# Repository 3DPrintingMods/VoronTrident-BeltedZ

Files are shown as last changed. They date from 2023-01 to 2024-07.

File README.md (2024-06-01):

<br/>
<p align="center">
  <h3 align="center">Voron Trident Belted Z</h3>

  <p align="center">
    Belt all the things.
    <br/>
    <br/>
  </p>
</p>

## About The Project

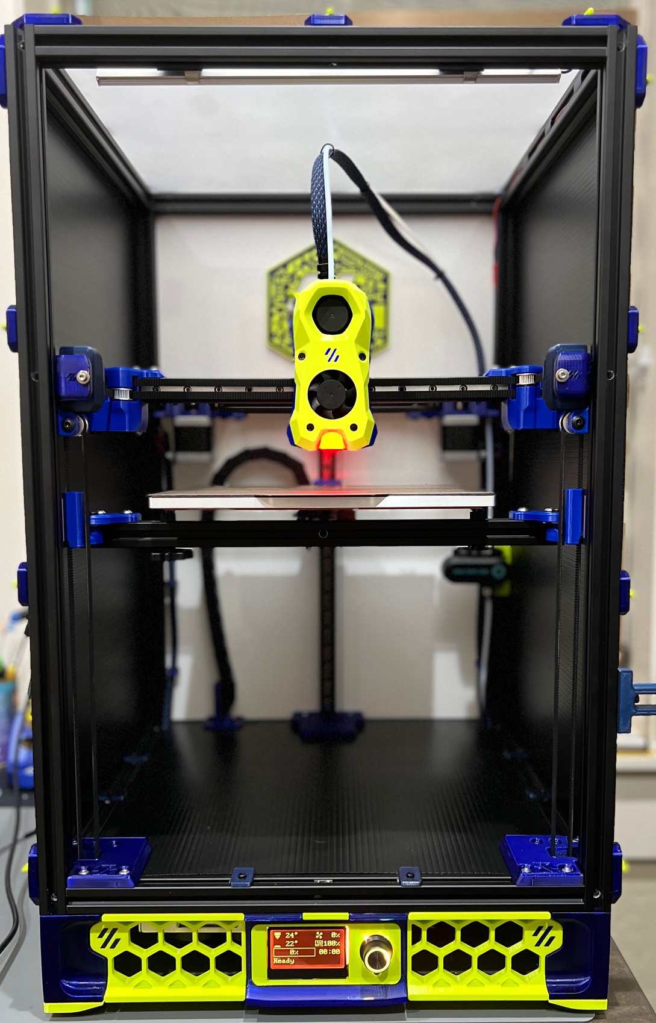
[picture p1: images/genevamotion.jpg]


This `mod` is the combination of multiple ideas for belted system for the Trident Z motion. Most of the inspiration came from X0, which uses NEMA 17 gearboxes. The main goal was to use 9mm belts for Z motion while keeping most of the original Trident skirts and not relocating Z steppers to the top of the printer. We give credit to `bythorsthunder` for his [Orion belted mod](https://github.com/bythorsthunder/Orion-Tri-Belt), which has also been proven efficient and easy to assemble (the same applies to the [belted z motion](https://github.com/MathematicalPotato/Voron_Mods/tree/main/VT_Belted_Z) mod introduced by `MathematicalPotato`).

## General Info

The design offers two different options for the Z idlers:

MathmaticalPotato Idlers: 
 - Uses existing XY front idlers
 - Limited to ONLY 9mm wide pulleys (12mm overall width)
<p align="left">
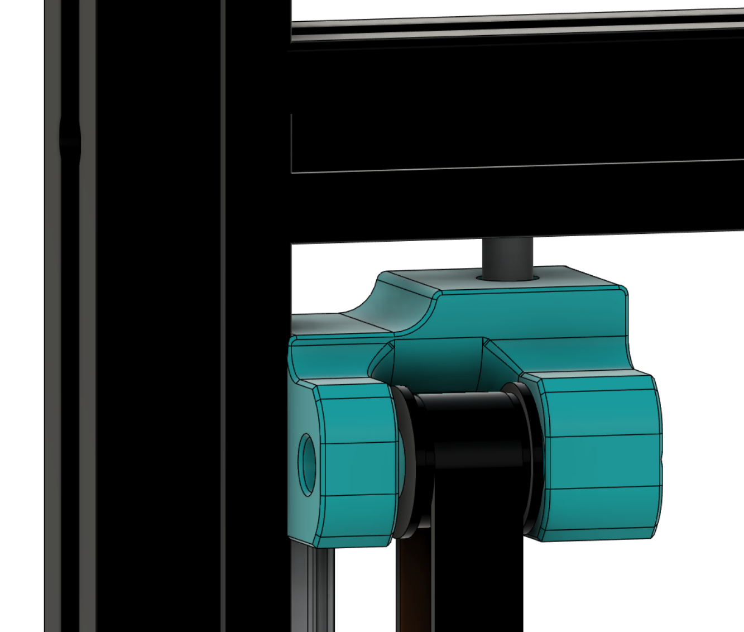
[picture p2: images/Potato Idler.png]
  
</p>

DoubleT XYZ Idlers:
 - Modified version of the Ramalama2 idler design
 - Z idler pulley integrated into XY idler
 - More flexibility in Z pulley width
<p align="left">
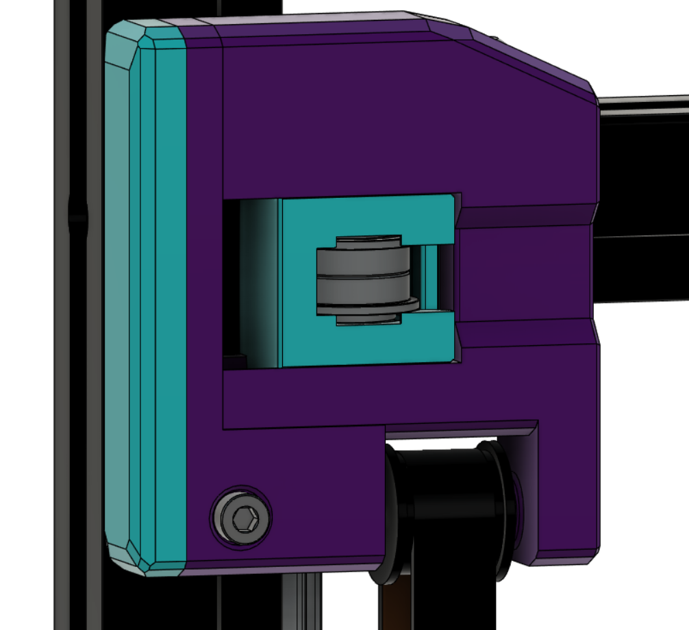
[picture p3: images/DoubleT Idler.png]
  
</p>

Refer to the CAD drawing for detail on both Idlers.
BOM contains sections for both.

## Update History:

#May 31st 2024
 - Added motor mounts and skirts for larger gearbox 'precision' motors
 - NOTE:  These motors are recommended for larger bed sizes 300+
 - Added Z idlers for DoubleT / Fabreeko 9MM metal gantry

#April 2024
 - Monolith Gantry Support added

#November 30th 2023
 - V2 Beta idlers added

#October 12th 2023
 - Raised the bed standoffs on the carriages by 6mm.
 - This should improve compatibility with slimmer beds and most iterations of Tiny-T.
 - NOTE: Requires a change from M5x16 to M5x25 fasteners for the carriage to the bed frame.

#July 23rd 2023 
 - Added belt/stepper covers for inverted electronics by `Panzarkatten`

#July 3rd 2023:
 - Revised rear motor mount and idler.  Orientation of the motor turned 90 degrees. New idler replaces the rear bracing from Z extrusion to A/B drive extrusion
 - New front idler option added. Integrated the Z idler pulley into DoubleT's modified Rama idlers.
 - Cleaned up the CAD
 - Added motor skirts for 350mm build size

## Tiny-T considerations:
The Tiny-T supports the use of either MGN9 or MGN12 linear guides on the X axis.  This mod is compatible with MGN12 / Afterburner/Stealthburner style toolheads without modificaiton.
MGN9 based systems using V0.2 style toolheads will position the nozzle 5-6mm higher than AB/SB configurations.  This results in the bed being unable to reach the nozzle before colliding with the Z idlers. V3 Z carriages should resolve this travel limitation, but this assumes the use of a 6mm build plate with a 1mm magnet.  Magbeds may need additional spacing.

## Bill Of Materials

#Required parts:

- 3 NEMA 17 Precision planetary steppers
	 - Recommended for larger bed sizes.
	 - Higher Gear Ratio, lower backlash
	 - [OMC Stepperonline](https://www.omc-stepperonline.com/nema-17-stepper-motor-l-40mm-gear-ratio-10-1-mg-series-planetary-gearbox-17hs15-1584s-mg10)
*or*
- 3 NEMA 17 Economy planetary steppers
	- [Ali Express](https://www.aliexpress.us/item/3256804434852612.html)
	- [Amazon](https://www.amazon.com/STEPPERONLINE-Planetary-Gearbox-Stepper-Printer/dp/B00WATUFIG)

- 9mm GT2 belts
- 3 9mm 20T GT2 drive pulleys, 8mm ID
- 3 9mm 20T toothed idlers, 5mm ID - Gates/Runice recommended. (Overall width of less than 14mm, Flange diameter less than 16mm)
- 9 M3x12 Button head screws (mounting gearmotors)
- 8 M3x30 Socket head screws (Front Motor Bracing, Rear Z carriage mounting)
- 2 M3x35 screws (Front Z belt tensioners)
- 1 M3x40 screw (Rear Z belt tensioner)
- 7 M3 heatset inserts (Front motor bracing, Z belt tensioners)
- 2 M5x35 screws and nuts (front idlers)
- 1 M5x25 screw and nut (rear idler)
- 1 5mmx30mm dowel (Rear Z Idler Shaft)
- 20 M5x10 screws and hammerhead nuts for mounting motor mounts and idlers
- 1 M3 x ? length screw - Length determined by motor chosen. Remove one screw from the nema17 motor housing and replace with longer screw for the rear motor stabilizer.
- 3 M5x25 BHCS - Z carriage to bed frame

<p align="left">
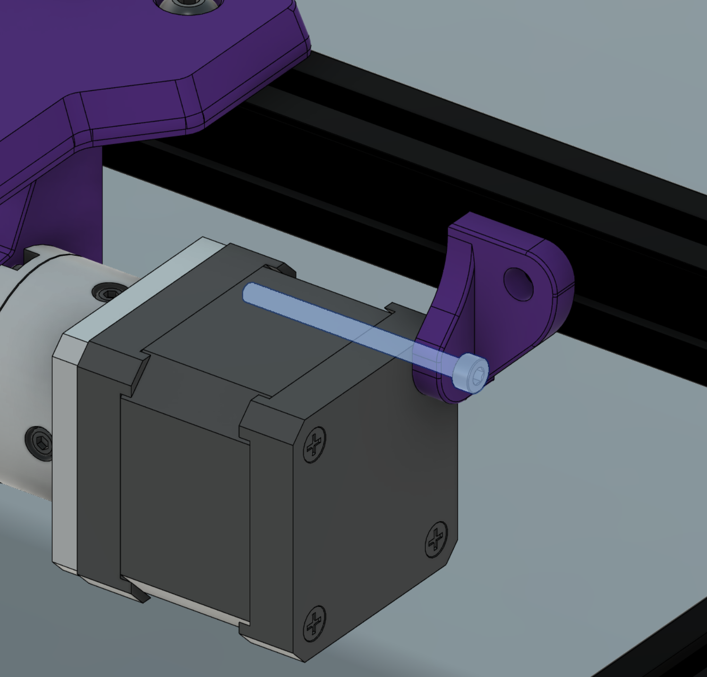
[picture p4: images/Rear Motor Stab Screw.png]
  
</p>

Mathematical Potato Idlers:
- 2 M4x20 Socket head screws and hammerhead nuts
- 2 M5x40 Button head screws
- 2 M5 nuts
- 2 M5x15 Button Head Screws

DoubleT XYZ Idlers
 - Reuses existing fasteners for securing idler to Y extrusion
- 4 M3 heatset inserts
- 4 M3x30 Button head screws
- 2 M3x12 Socket head screws
- 2 M3x20 Socket head screws and hammerhead nuts
- 2 5mm x 25mm dowel
- 2 5mm x 20mm dowel
- 4 6mm x 3mm magnets

## Authors

* **genevamotion** - ** - [genevamotion](https://github.com/tdlane1) - *CAD design/ Modeling / Testing*
* **thiagolocatelli** - ** - [thiagolocatelli](https://github.com/thiagolocatelli) - *CAD design / Modeling / Project Management*

## Acknowledgements

* [MathematicalPotato](https://github.com/MathematicalPotato)
* [bythorsthunder](https://github.com/bythorsthunder)
* [Annex Engineering](https://github.com/Annex-Engineering)
* [Voron Design](https://github.com/VoronDesign)
* [Ramalama](https://github.com/Ramalama2)
* [clee](https://github.com/clee/VoronBFI)

## Images

<p align="center">
  
</p>

<p align="center">
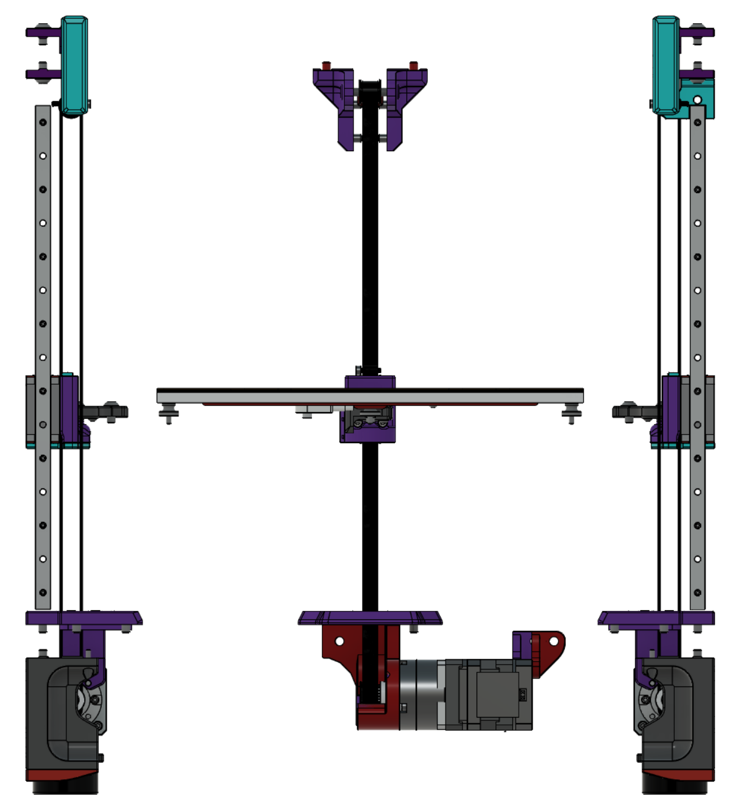
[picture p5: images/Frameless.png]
  
</p>

<p align="center">
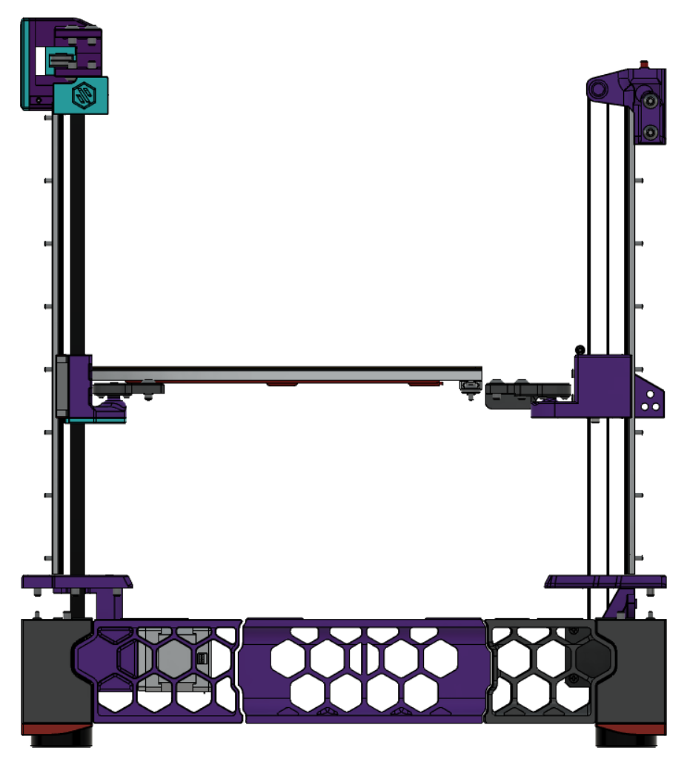
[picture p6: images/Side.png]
  
</p>

<p align="center">
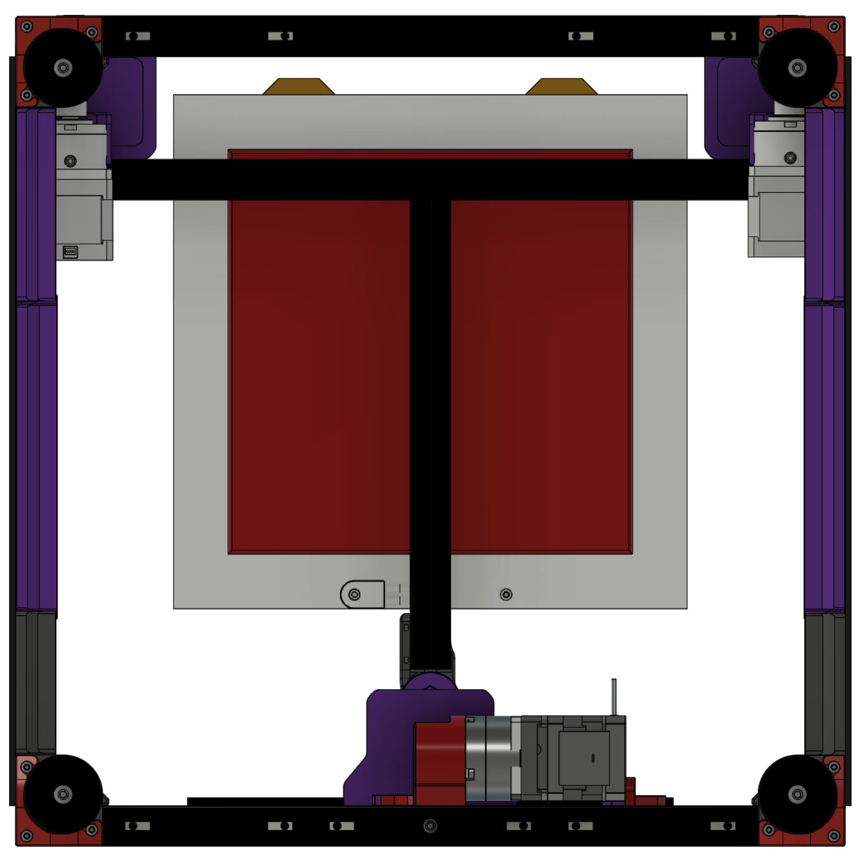
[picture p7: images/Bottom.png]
  
</p>

<p align="center">
  
</p>

## Sample config (Manta M8P) - Economy Gearbox 

```
[stepper_z]
step_pin: ###
dir_pin: ###
enable_pin: ###
rotation_distance: 40
gear_ratio: 57:11   
microsteps: 32
endstop_pin: ###

##  Make sure to update below for your relevant driver (2208 or 2209)
[tmc2209 stepper_z]
uart_pin: ###
interpolate: False
run_current: 1.0
sense_resistor: 0.110
stealthchop_threshold: 0

```

# Builds

## Panzarkatten

<p align="center">
  
</p>

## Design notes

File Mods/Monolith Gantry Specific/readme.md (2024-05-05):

## BeltedZ components for Monolith Gantry

These parts were created for compatibility with [Monolith Gantry](https://github.com/CloakedWayne/Monolith_Gantry_V2-VT).  No changes are needed to the monolith gantry components. The mod includes modified Z idlers and *optional* Z carriages that relocate the bed 10mm in the +Y direction.  

The Notes and BOM differences may leave out critical information. These BOM differences are in relation to the BeltedZ mod, and not stock Voron components.  Apologies in advance if items were left out.

I'm lazy - Printing orientation has not been preset on many parts, but it's fairly obvious in most cases which side is down.

## Idler Notes

 - The front Z idlers currently use M5x45 screws as shafts for the idler pulleys to ride on.  This isn't a perfect solution, and a dowel-pin version is on the horizon.
 - The front Z linear guides will obstruct insertion and removal of the front-most fasteners that secure the idlers to the Y extrusions.  It is recommended that you install the front XY and Z idler assemblies **before** the Y linear guides.  This will allow the idler assembly to be slid along the Y extrusion for access to insert the fastener, and slid back into place for before final tightening of the fasteners.  Alternatively, you can remove the Z linear guide for access, but in most cases you will already have the Y linear guides removed during conversion to Monolith Gantry.
 - The rear Z idler has notches for the Monolith AB tensioners to clear, as well as provide access to the tensioning screws. These notches aren't needed in 250+ builds, but with Tiny-T they are necessary.
 - AWD idler spacers are provided.  These are needed to space the Z idler lower so that it can clear the shear support plates of the front motor mounts. Longer fasteners are needed to secure the idlers to the Y extrusions.
 - You may notice the front Z idlers have a circular relief in the top side that goes nowhere. This is to provide clearance for a fastener that may be present on the monolith front motorless mounts. BHCS is assumed in this case, and the fastener may need to be changed to fit the relief.

**Idler BOM Differences**

 - Idlers (2WD):
	 - 4x M5x16 
	 - 2X M5x20
	 - 2X M5x45

- Idlers (AWD):
	- 6x M5x20
	- 2X M5x45

## Bed +10 Notes
*Why relocate the bed?* - This isn't necessary, but some toolhead designs will place the hotend nozzle as close to the X axis linear rail carriage as possible to improve balance and center of mass. The front edge of the bed may be out of reach with stock carriages in this scenario.

 - A modified Z_Bed_Rear model is provided.  This part needs to be printed, as the stock Voron rear bed extrusion attachement interferes with the belt.  It has clearance for the belt as well as relocated fasteners that secure the spherical bearing to the part.
 - Z carriages elevate the bed 5mm over stock to reach PFA style toolheads on Tiny-T.  Verify total Z travel distance after completion as the new carriages have probably affected it.

**Z Carriage BOM Differences**

 - 4x M3x20
- 8x M3x25
- 3x M5x25

## Acknowledgements:

 - The BeltedZ mod was heavily inspired by MathematicalPotato's [VT_Belted_Z](https://github.com/MathematicalPotato/Voron_Mods/tree/main/VT_Belted_Z) mod
 - [CloakedWayne](https://github.com/CloakedWayne) - Monolith Gantry

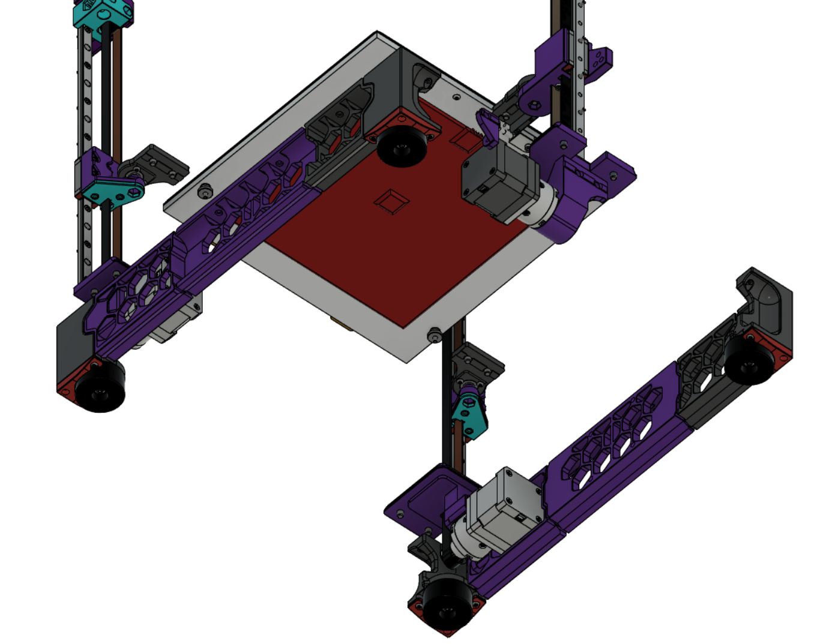
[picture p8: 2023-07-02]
images/Bottom Iso.png

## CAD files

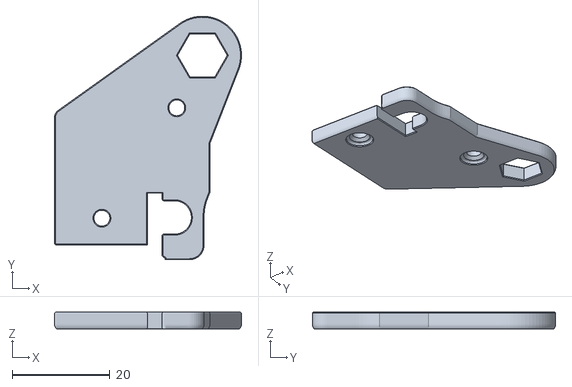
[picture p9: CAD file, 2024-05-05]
Mods/Monolith Gantry Specific/STL/Bed_Plus_10MM/Z_Carriage_Accent_L.stl
38.2 x 49.8 x 3.45

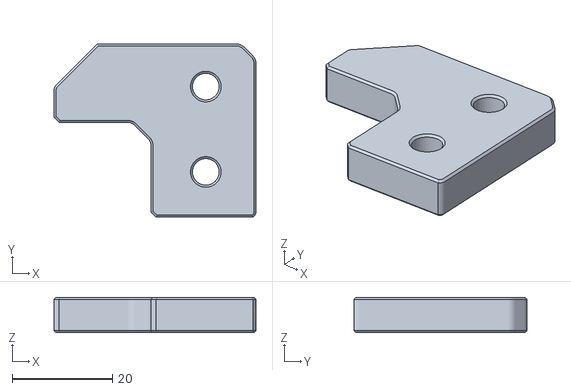
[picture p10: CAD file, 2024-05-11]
Mods/Monolith Gantry Specific/STL/Z_Idlers/Idler_Spacer_AWD9MM (x2).stl
40.2 x 34.5 x 7.00

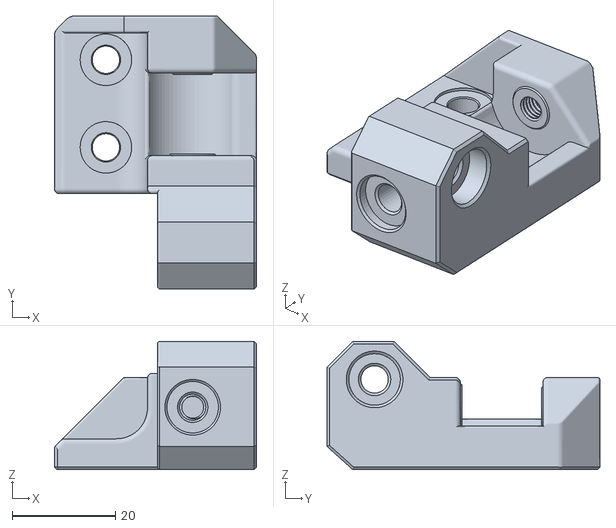
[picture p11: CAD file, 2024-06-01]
Mods/Z Idlers for DoubleT CNC 9MM gantry/Front_Z_Idler_DoubleT9mm_Right.stl
39.2 x 53.0 x 24.9

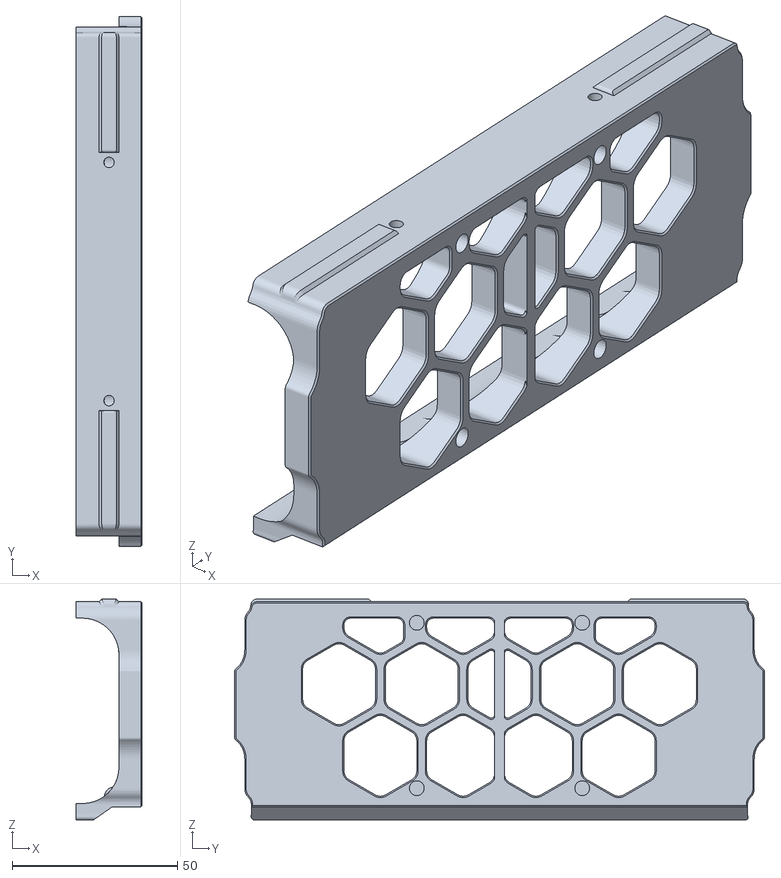
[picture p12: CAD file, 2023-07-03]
STLs/Economy Motor Skirts 250_300/mid_skirt_250only.stl
20.0 x 160.2 x 66.8

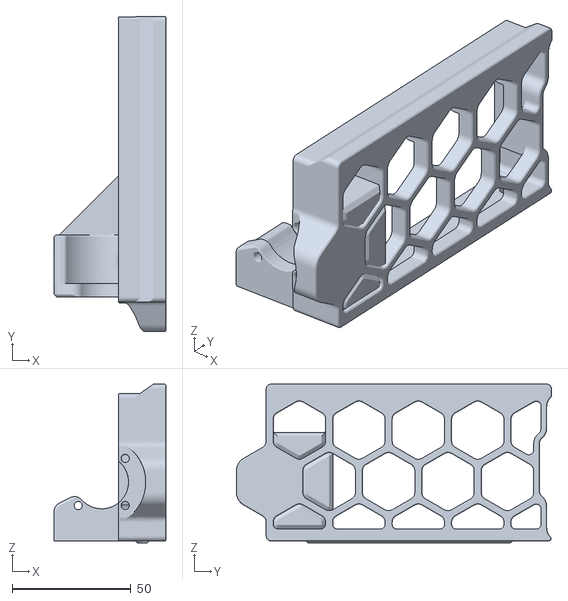
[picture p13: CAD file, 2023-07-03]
STLs/Economy Motor Skirts 350/z_motor_skirt_left_350.stl
47.1 x 132.5 x 66.8

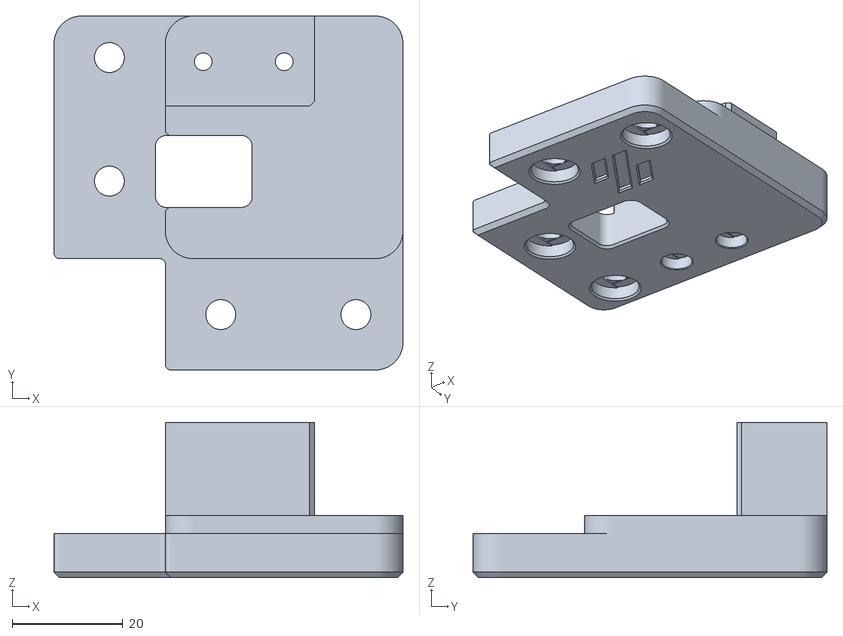
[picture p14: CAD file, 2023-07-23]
STLs/Inverted Electronics/Right_Motor_Cover_Inv.stl
63.0 x 63.9 x 28.0

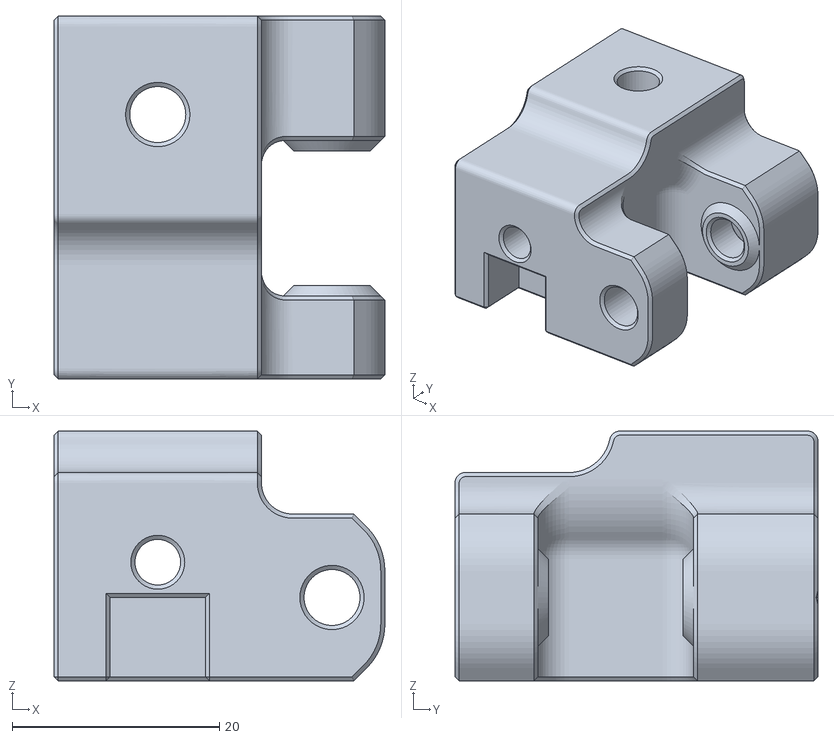
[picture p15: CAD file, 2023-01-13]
STLs/MathematicalPotato Z Idlers/z_idler_mount_left.stl
31.9 x 35.0 x 24.1

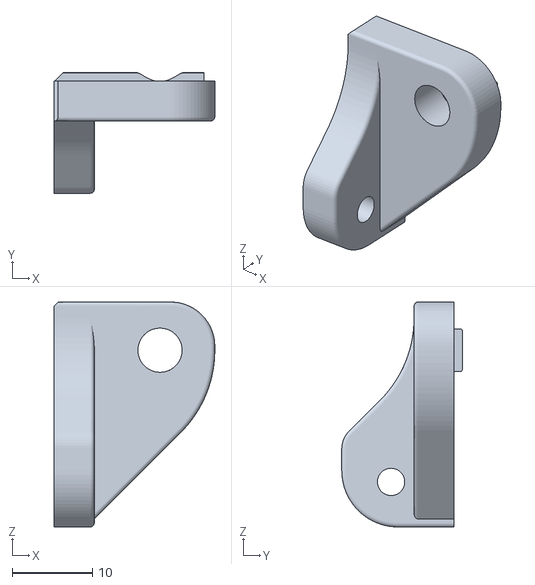
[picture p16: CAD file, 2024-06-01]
STLs/Precision Motor Mount Rear/Rear Motor Supplemental Support.stl
20.0 x 15.0 x 28.0

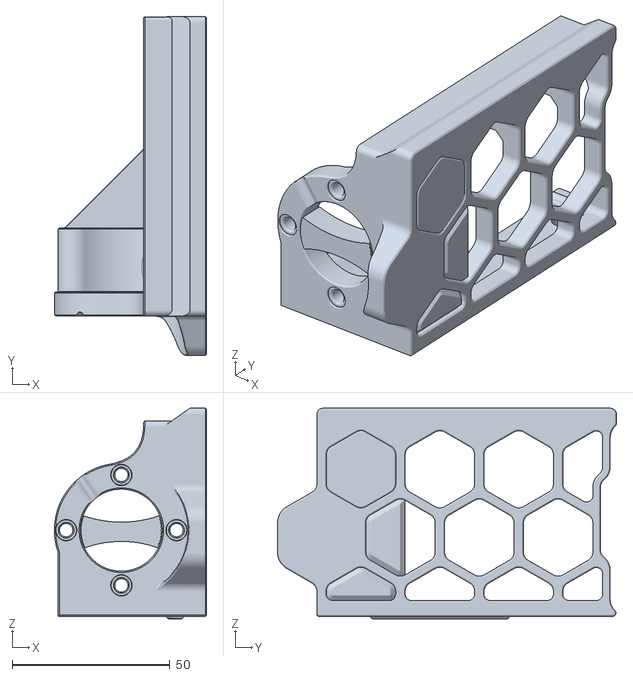
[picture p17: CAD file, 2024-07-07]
STLs/Precision Motor Skirts 250_300/Precision_Motor_Skirt_Left_250_300.stl
48.3 x 107.5 x 66.8

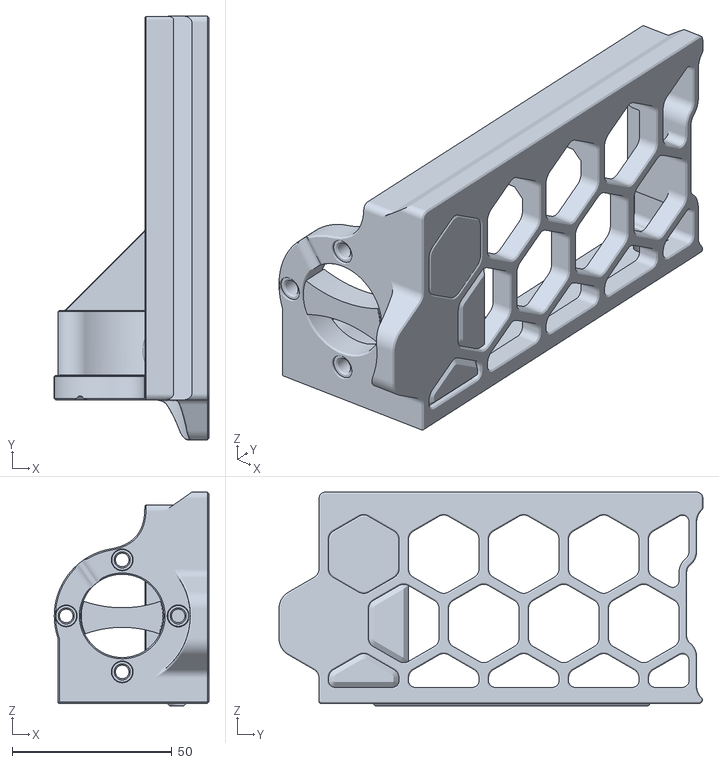
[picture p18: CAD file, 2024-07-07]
STLs/Precision Motor Skirts 350/Precision_Motor_Skirt_Left_350.stl
48.3 x 132.5 x 66.8

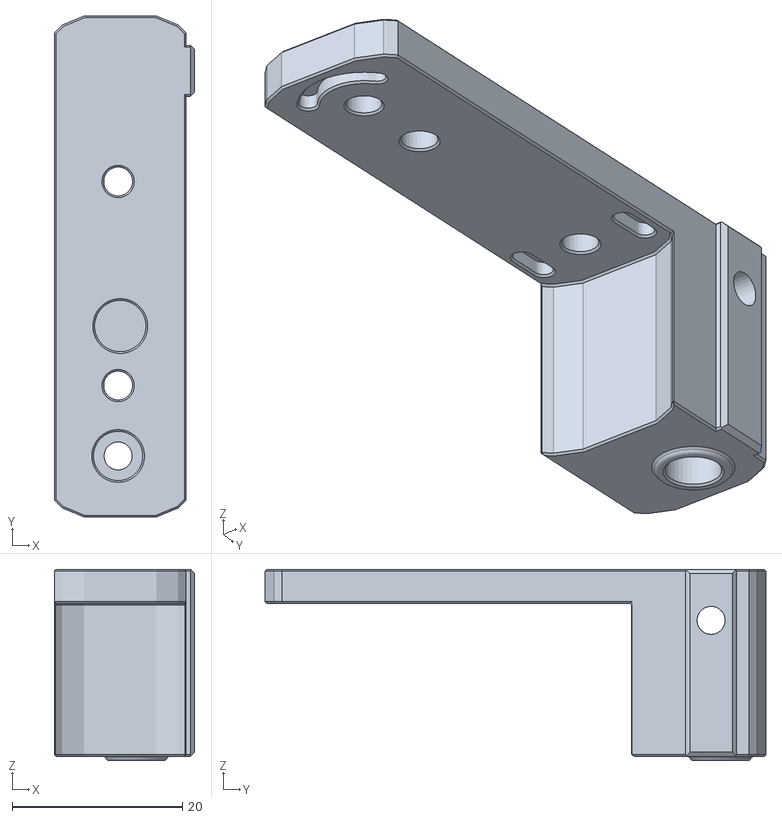
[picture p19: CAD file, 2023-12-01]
STLs/V2_DoubleT XYZ Idlers/left_idlerhousing_front_v2.stl
16.5 x 58.9 x 22.5

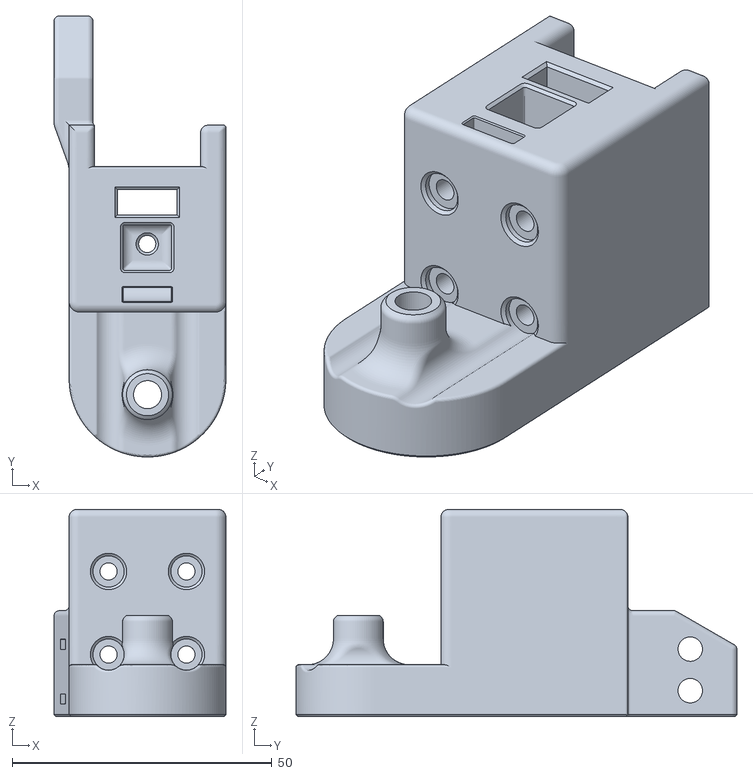
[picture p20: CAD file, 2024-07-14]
STLs/z_carriage_rear_2_Hole_V4.stl
33.1 x 84.9 x 39.9

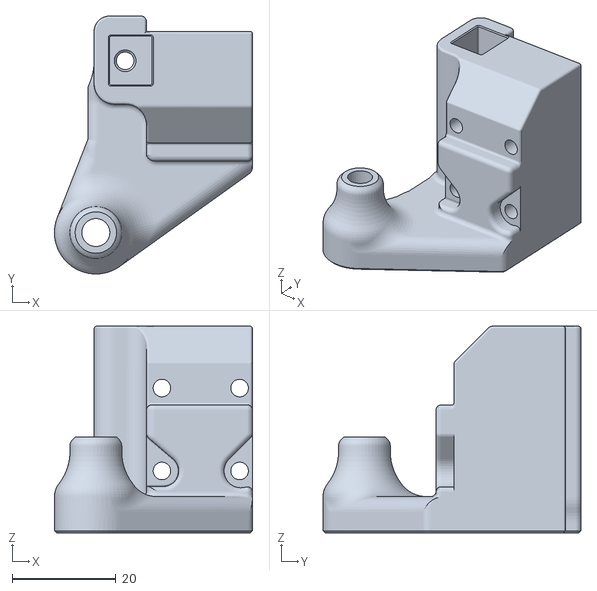
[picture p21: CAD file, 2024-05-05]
Mods/Monolith Gantry Specific/STL/Bed_Plus_10MM/Z_Carriage_Left_10MM.stl
38.2 x 49.8 x 39.9

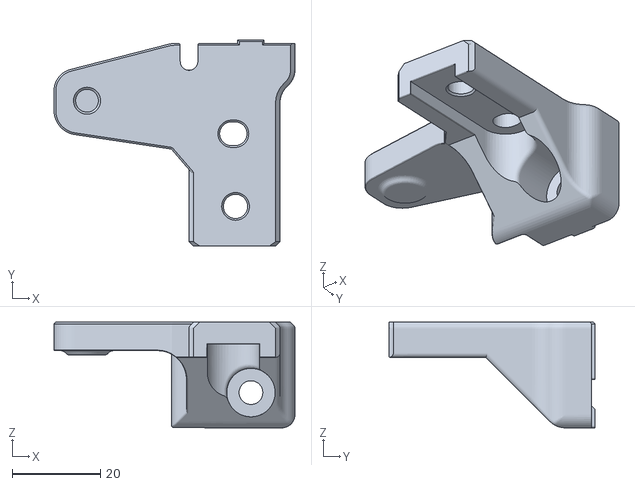
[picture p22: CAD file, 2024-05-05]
Mods/Monolith Gantry Specific/STL/Z_Idlers/Rear_Z_Idler_Brace_Monolith_B.stl
54.7 x 46.8 x 24.0

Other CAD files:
Mods/Z Idlers for DoubleT CNC 9MM gantry/Front_Z_Idler_DoubleT9mm_Left.stl
STLs/Economy Motor Skirts 250_300/z_motor_skirt_right_V2.stl
STLs/Economy Motor Skirts 350/z_motor_skirt_right_350.stl
STLs/Inverted Electronics/Rear_Motor_Cover_Inv.stl
Mods/Monolith Gantry Specific/STL/Bed_Plus_10MM/Z_Bed_Rear_10MM.stl
Mods/Monolith Gantry Specific/STL/Bed_Plus_10MM/Z_Carriage_Accent_R.stl
Mods/Monolith Gantry Specific/STL/Bed_Plus_10MM/Z_Carriage_Rear_10MM.stl
Mods/Monolith Gantry Specific/STL/Bed_Plus_10MM/Z_Carriage_Right_10MM.stl
Mods/Monolith Gantry Specific/STL/Z_Idlers/FrontZIdlerMonolith_Screw_Left.stl
Mods/Monolith Gantry Specific/STL/Z_Idlers/FrontZIdlerMonolith_Screw_Right.stl
Mods/Monolith Gantry Specific/STL/Z_Idlers/Idler_Spacer_AWD6MM (x2).stl
Mods/Monolith Gantry Specific/STL/Z_Idlers/Rear_Z_Idler_Brace_Monolith_A.stl
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

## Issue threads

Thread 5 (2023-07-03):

Z Motor Skirts L&R for 350?

Killajoedotcom, 2023-07-03:
Is there a chance you could make the Z motor skirt mounts for a 350 sized Trident? I'm thinking the current set only fit a 250.

tdlane1, 2023-07-03:
I can work on this.  The current design used the 300mm front skirts as a base model for the motor skirts.  250 compatibility is provided by the modified midskirts in the CAD.  Extension of the existing motor skirts to 350mm size should be all that's needed.

Killajoedotcom, 2023-07-03:
That's great! Thanks so much. Keen to get this installed because I'm rebuilding the Trident anyway.

thiagolocatelli, 2023-07-03:
@Killajoedotcom @tdlane1 has just added the skirts. Tweet some pictures once you rebuild the Trident.

Killajoedotcom, 2023-07-03:
> @Killajoedotcom @tdlane1 has just added the skirts. Tweet some pictures once you rebuild the Trident.

Will do! I'll tag you both!

Closed 2023-07-03.

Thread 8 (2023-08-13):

idler_housing_front_right.stl wrong dowel hole location

Pockrandt, 2023-08-13:
[idler_housing_front_right.stl](https://github.com/3DPrintingMods/VoronTrident-BeltedZ/blob/master/STLs/DoubleT%20XYZ%20Idlers/idler_housing_front_right.stl) has the hole for the dowel on the wrong side.

The CAD is correct.
Also the name is weird as this one is on the left side when the printer is in front of you.

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

Closed 2023-08-13.

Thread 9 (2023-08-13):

Champfer on z_carriage_left & z_carriage_right

Pockrandt, 2023-08-13:
Thanks for fixing the screw holes, mind also moving the champfer?

[z_carriage_left.stl](https://github.com/3DPrintingMods/VoronTrident-BeltedZ/blob/master/STLs/z_carriage_left.stl)
[z_carriage_right.stl](https://github.com/3DPrintingMods/VoronTrident-BeltedZ/blob/master/STLs/z_carriage_right.stl)

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

Closed 2023-08-13.

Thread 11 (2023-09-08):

Right Idler Housing pins do not line up.

timknab, 2023-09-08:
It looks like this was mentioned in #8 and supposedly fixed in #10 but it appears that the pins or dowels on the right idler assembly still do not line up.

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

In addition to the CAD, I verified that the STLs are also incorrect after printing them and finding that the pieces do not go together...

Closed 2023-09-12.

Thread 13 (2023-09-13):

Other version

pasha4ur, 2023-09-13:
Hello

Thank you.

Can you add in mod also support for regular motors with reduction like voron 2.4?

Other mods like Orion (incompatible with 4040 and 2040 t-slot profile) or VT_Belted_Z are unfinished or have bad design solutions. Your work looks more professional and thoughtful.

If you add 1mm everywhere we could use 10 mm betls and get +11% belt stiffness. All components except carriages are compatible with 10 mm belts.

This is important for very big build plates or with glass surface. I have 450mm trident with 4040/2040 t-slot frame.

tdlane1, 2023-09-15:
Hi Pavel,

Thanks for the positive feedback.  I'm glad you appreciate our work on this mod.  The primary goal of this mod was to minimize the disruption of the stock Trident skirts.  The gearmotors allow the front skirts to remain completely unchanged and reduce complexity and BOM items compared to the belt and pulley reduction used on the V2 style assemblies.

This mod was heavily inspired by MathematicalPotato's VT_Belted_Z mod, and borrows a lot of elements from it.

My recommendation if larger build surfaces are needed would be to increase the gear reduction.  OMC offers economy geared stepper motors with higher gear reduction.

I can investigate changes needed to accommodate 10mm belts and pulleys in the upcoming weeks.  Can you provide links to the pulleys and idler hardware you wish to use?

droidgee, 2023-10-08:
Along similar line, suggestions on what build plate would hold up ok with the 5:1 motors listed in the BOM?

Thinking of using this on a 300x300 build, not sure how thick of a plate to go with (before upping the gear reduction)

Thanks.

tdlane1, 2023-10-12:
@droidgee  - Apologies for the delayed reply.  Feedback and testing has only been provided for bed sizes 250mm and below.  I can't say for sure that the 5.18:1 motors specified in the bom can support a 300mm bed without sag.  Increasing the gear ratio would certainly help to avoid bed sag, but the motor skirts have limited clearance for motor length.  Give me some time to investigate whether the 19:1 economy motors (OMC 17hs15-1684s-pg27) will fit. If that isn't feasible, I'll look into modifying the design to accommodate the 10:1 precision planetary motors from OMC.  I've tested those motors with an 8mm build plate and they do not backdrive from the bed weight.

FabianFloss, 2024-07-06:
Heyy  i found an Problem with the Precision Motors the Holes in the Stl Files are M3 Screws but in the Motors you linked to Stepper Online they have M4 maby you can change it thank you

tdlane1, 2024-07-07:
Hi @FabianFloss I've corrected the motor skirts and uploaded new models.   If you find another problem, please create a new issue, rather than commenting on this one.  Thanks for letting me know!

FabianFloss, 2024-07-07:
@tdlane1 thank you for fast changing👍

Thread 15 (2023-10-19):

Wrong rotation distance in a sample config

josef-jelinek, 2023-10-19:
The economy planetary gearboxes linked have true ratio of 57:11, which is rounded in descriptions to 5.18:1 (or sometimes even 5:1).
That means that for 20T 2GT, the real rotation distance is 40*11/57 which is about 7.7193.
The configuration shows 7.75, which would mean that the gear ratio is close to 5.16129:1.
It seems like this disparity should be subtracting about 0.03mm each rotation resulting in close to 1mm subtracted from 250mm maximum print height.

After I wrote above, I found out that this exact case is described in klipper docs and can be set precisely using gear_ratio to the one above: https://www.klipper3d.org/Rotation_Distance.html#using-a-gear_ratio

tdlane1, 2023-10-22:
Thanks for pointing this out.  I've updated the example config with new rotation distance and gear ratio.

Closed 2023-10-22.

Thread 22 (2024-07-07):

Heyy  i found an Problem with the Precision Motors the Holes in the Stl Files are M3 Screws but in the Motors you linked to Stepper Online they have M4 maby you can change it thank you

tdlane1, 2024-07-07:
Heyy  i found an Problem with the Precision Motors the Holes in the Stl Files are M3 Screws but in the Motors you linked to Stepper Online they have M4 maby you can change it thank you

_Originally posted by @FabianFloss in https://github.com/3DPrintingMods/VoronTrident-BeltedZ/issues/13#issuecomment-2211971381_

tdlane1, 2024-07-07:
Apologies for that.  I updated the motor skirts for the correct fastener size.

Closed 2024-07-07.

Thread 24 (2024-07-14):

VT rear Z carriage -- 2 hole chain support

slashbeast, 2024-07-14:
Hi,

Would you consider adding variant of rear Z carriage that have support for 2 hole chains?

Thanks.

tdlane1, 2024-07-14:
Done!  Thanks for pointing this one out.

Closed 2024-07-14.

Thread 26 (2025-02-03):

Mgn12h

Moneyshot69, 2025-02-03:
Hi I was wondering if this could be used with mgn12h rails for Z as I plan to have a 600mm Z and wanted to use bigger linear rails than mgn9h for a higher Z. Is there any chance of modifying the files to accommodate mgn12h or will they not work with bigger linear rails. Thanks for your time and effort

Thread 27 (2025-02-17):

Config for specified precision motors

axg20202, 2025-02-17:
Is there a config example available with the correct gear ratios for these motors please?

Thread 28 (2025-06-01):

Misalignment of frame profiles in CAD

maxmadzz, 2025-06-01:
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

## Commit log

2023-01-13 Initial Release
    [z_carriage_left_belt_tensioner.stl, z_carriage_rear.stl, z_carriage_right_belt_tensioner.stl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]
2023-01-23 Version 2 updates
    Updates:
    - Updated BOM with additional items
    CAD changes:
    - Revised front motor skirts and motor covers to add additional bracing via two M3x30 screws in each motor mount
    - Increased size of front belt tensioners to ensure adequate engagement with belt teeth.
    STL Changes:
    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
    [(a)z_carriage_accent_left.stl, (a)z_carriage_accent_right.stl, z_belt_tensioner_front_V2-x2.stl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]
2023-06-06 Z Carriage corrections
    Hole spacing on Z carriages was wrong. Modified hole spacing to correctly mount to MGN9 carriage.
2023-06-23 Update z_motor_mount_rear.stl
    Modified rear Z motor mount to fit stock trident deck panel
2023-07-02 July 2nd update - New Rear Z and updated idlers!
    - Added rear Z configuration from the sidepack build
    - Added integrated XYZ idlers from the sidepack build
    - Updated BOM and Readme with more stuff
    - Updated STL's and CAD
    [(a)idler_cover_left.stl, (a)idler_cover_right.stl, (a)idler_inlet_left.stl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]
2023-07-03 350mm motor skirts added
    [mid_skirt_250only.stl, z_motor_skirt_left_350.stl, z_motor_skirt_left_V2.stl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]
2023-07-17 Corrections
    Right Side Double-T idler assembly was incorrect (mirror of left, incorrect belt alignment).
    Remodeled the idler.
    Updated CAD and Idler STLS added to repo
    [(a)idler_cover_right.stl, (a)idler_inlet_right.stl, idler_housing_front_right.stl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]
2023-07-23 Added inverted electronics belt covers
    [Left_Motor_Cover_Inv.stl, Rear_Motor_Cover_Inv.stl, Right_Motor_Cover_Inv.stl]
2023-08-13 Fixes for Issue #8 & #9
    - Corrected chamfer locations on front Z carriages
    - Less confusing naming for the doubleT idler components
    - new STL's for idlers and front Z carriages.
    [(a)idler_inlet_left.stl, (a)idler_inlet_right.stl, (a)idler_shuttle_left.stl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]
2023-09-09 Fixed right idler housing pin missalignment
    [right_idlerhousing_front.stl, right_idlerhousing_rear.stl]
2023-10-12 Z Carriage updates
    Raised bed standoffs by 6mm on Z carriages
    [z_carriage_left_V2.stl, z_carriage_rear_V2.stl, z_carriage_rear_V3.stl]
2023-10-22 Update README.md
    Modified example config for corrected rotation distance and gear ratio.
2023-12-01 V2 Beta Idlers
    Revised CAD and version 2 of the DoubleT XYZ idler models uploaded. BETA only, tested in one scenario.
    [(a)_idler_cover_right_v2.stl, (a)idler_cover_left.stl, (a)idler_cover_left_v2.stl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]
2024-05-05 Adding Monolith Mods
    Monolith Stuff!
    [FrontZIdlerMonolith_Screw_Left.stl, FrontZIdlerMonolith_Screw_Right.stl, Idler_Spacer_AWD (x2).stl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]
2024-05-11 Added 9mm AWD monolith spacers
    Monolith mods changes
    [Idler_Spacer_AWD6MM (x2).stl, Idler_Spacer_AWD9MM (x2).stl]
2024-06-01 Updates for precision motors
    Precision motor mounts added, DoubleT 9mm CNC gantry idlers added
    [(a)_idler_cover_right_v2.stl, (a)idler_cover_left_v2.stl, (a)idler_shuttle_v2_x2.stl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]
2024-06-01 Minor change to DoubleT metal gantry idlers
    Screw head pocket
    [Front_Z_Idler_DoubleT9mm_Left.stl, Front_Z_Idler_DoubleT9mm_Right.stl, Spacer_9_5_x_3_5 (x4).stl]
2024-07-04 Adding Rear Idlers / Updated Rear Carriage
    Adding modified Rear Z Idler assembly for 9mm belt clearance
    V4 Rear carraige - Increased the size of the belt pathway to make threading the belt though the carriage a bit easier.
    [Front_Z_Idler_DoubleT9mm_Left.stl, Front_Z_Idler_DoubleT9mm_Right.stl, Spacer_9_5_x_3_5 (x4).stl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]
2024-07-07 Corrected Precision Motor Skirts
    Wrong size fastener holes - Fixed to accommodate M4 fasteners. Genevamotion can't read drawings well.
    [Precision_Motor_Skirt_Left_250_300.stl, Precision_Motor_Skirt_Left_350.stl, Precision_Motor_Skirt_Right_250_300.stl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]
2024-07-14 2 hole rear carriage added
    Adding 2 hole rear carriage - Issue #24
    [z_carriage_rear_2_Hole_V4.stl, z_carriage_rear_3_hole_V4.stl, z_carriage_rear_V4.stl]
